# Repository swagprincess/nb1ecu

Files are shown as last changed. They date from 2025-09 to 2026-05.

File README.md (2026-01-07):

# A Speeduino Teensy 4.1 ECU For a NB1 Miata #

Integrated Wideband controller (Spartan 3 OEM), MAP and everything needed for it to be PNP.

Using the current fastest Speeduino brain (Teensy 4.1 600MHz).

Config is a modified init.cpp pinmapping case 56 "Bear Cub", adds default pins for features like AC control

Speeduino.ini for TunerStudio is Case 56, changed name to SwagPrincess NB1 PNP

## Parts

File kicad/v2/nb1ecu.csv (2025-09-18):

Reference | Qty | Value | DNP | Exclude from BOM | Exclude from Board | Footprint | Datasheet | LCSC Part #
C1,C7 | 2 | 100u |  |  |  | Capacitor_THT:CP_Radial_D6.3mm_P2.50mm | ~ | C109392
C2,C21 | 2 | 22n |  |  |  | Capacitor_SMD:C_0805_2012Metric_Pad1.18x1.45mm_HandSolder | ~ | C77069
C3 | 1 | 1n |  |  |  | Capacitor_SMD:C_0805_2012Metric_Pad1.18x1.45mm_HandSolder | ~ | C1791
C4,C6 | 2 | 10u |  |  |  | Capacitor_SMD:C_0805_2012Metric_Pad1.18x1.45mm_HandSolder | ~ | C84416
C5,C8,C13,C15,C18,C19,C20 | 7 | 100n |  |  |  | Capacitor_SMD:C_0805_2012Metric_Pad1.18x1.45mm_HandSolder | ~ | C520083
C9,C10,C12,C14,C16,C17 | 6 | 220n |  |  |  | Capacitor_SMD:C_0805_2012Metric_Pad1.18x1.45mm_HandSolder | ~ | C541527
C11 | 1 | 470n |  |  |  | Capacitor_SMD:C_0805_2012Metric_Pad1.18x1.45mm_HandSolder | ~ | C520079
L1 | 1 | 4.7u |  |  |  | Inductor_SMD:L_1008_2520Metric_Pad1.43x2.20mm_HandSolder | ~ | C82314
P2 | 1 | 178780-1 |  |  |  | 178780-1 | DOCUMENTATION | C5166246
Q1,Q2 | 2 | PN2907A |  |  |  | Package_TO_SOT_THT:TO-92_Inline_Wide | https://www.nteinc.com/specs/original/2N3905_06.pdf | C513106
Q3,Q4,Q5,Q8,Q9,Q10,Q11,Q12,Q13,Q14,Q15,Q16,Q17 | 13 | DMG2302U |  |  |  | Package_TO_SOT_SMD:SOT-23 | http://www.diodes.com/assets/Datasheets/DMG2302U.pdf | C96613
Q6 | 1 | DMG2305UX |  |  |  | Package_TO_SOT_SMD:SOT-23 | ~ | C150470
R1,R13 | 2 | 48.7k |  |  |  | Resistor_SMD:R_0805_2012Metric_Pad1.20x1.40mm_HandSolder | ~ | C865519
R2 | 1 | 330 |  |  |  | Resistor_SMD:R_0805_2012Metric_Pad1.20x1.40mm_HandSolder | ~ | C105878
R3 | 1 | 3.3k |  |  |  | Resistor_SMD:R_0805_2012Metric_Pad1.20x1.40mm_HandSolder | ~ | C114531
R4,R7 | 2 | 3k |  |  |  | Resistor_SMD:R_0805_2012Metric_Pad1.20x1.40mm_HandSolder | ~ | C126350
R5 | 1 | 30k |  |  |  | Resistor_SMD:R_0805_2012Metric_Pad1.20x1.40mm_HandSolder | ~ | C126352
R6,R32,R36,R37,R51 | 5 | 1k |  |  |  | Resistor_SMD:R_0805_2012Metric_Pad1.20x1.40mm_HandSolder | ~ | C727989
R8,R11,R12,R14,R33,R34,R35,R45 | 8 | 10k |  |  |  | Resistor_SMD:R_0805_2012Metric_Pad1.20x1.40mm_HandSolder | ~ | C855098
R9 | 1 | 1M |  |  |  | Resistor_SMD:R_0805_2012Metric_Pad1.20x1.40mm_HandSolder | ~ | C107700
R10 | 1 | 22k |  |  |  | Resistor_SMD:R_0805_2012Metric_Pad1.20x1.40mm_HandSolder | ~ | C114565
R15,R16,R17,R18,R20,R21,R23,R25,R27,R38,R39,R40,R43,R44,R46,R47 | 16 | 180k |  |  |  | Resistor_SMD:R_0805_2012Metric_Pad1.20x1.40mm_HandSolder | ~ | C865232
R19,R31,R50 | 3 | 470 |  |  |  | Resistor_SMD:R_0805_2012Metric_Pad1.20x1.40mm_HandSolder | ~ | C114564
R22,R24,R26,R28 | 4 | 348k |  |  |  | Resistor_SMD:R_0805_2012Metric_Pad1.20x1.40mm_HandSolder | ~ | C228757
R29,R30 | 2 | 2.49k |  |  |  | Resistor_SMD:R_0805_2012Metric_Pad1.20x1.40mm_HandSolder | ~ | C375522
R41,R42 | 2 | 220 |  |  |  | Resistor_SMD:R_0805_2012Metric_Pad1.20x1.40mm_HandSolder | ~ | C114519
R48 | 1 | 3.9k |  |  |  | Resistor_SMD:R_0805_2012Metric_Pad1.20x1.40mm_HandSolder | ~ | C865471
R49 | 1 | 604 |  |  |  | Resistor_SMD:R_0805_2012Metric_Pad1.20x1.40mm_HandSolder | ~ | C472205
U2 | 1 | TL431LP |  |  |  | Package_TO_SOT_THT:TO-92_Inline | http://www.ti.com/lit/ds/symlink/tl431.pdf | C398376
U4,U6 | 2 | TC4424AVOA |  |  |  | TC4424AVOA:SOIC127P599X175-8N |  | C44150
U5 | 1 | AP63205WU |  |  |  | Package_TO_SOT_SMD:TSOT-23-6 | https://www.diodes.com/assets/Datasheets/AP63200-AP63201-AP63203-AP63205.pdf | C2071056
U8 | 1 | MPXHZ6115A |  |  |  | Package_SO:SSOP-8_3.95x5.21x3.27mm_P1.27mm | https://www.nxp.com/docs/en/data-sheet/MPXA6115A.pdf | C3235759
U13 | 1 | LMV324LIDT |  |  |  | Package_SO:SOIC-14_3.9x8.7mm_P1.27mm | http://www.ti.com/lit/ds/symlink/lmv324.pdf | C262920
LAMBDA_OUT1 | 1 | TestPoint |  | Excluded from BOM |  | TestPoint:TestPoint_Pad_3.0x3.0mm | ~
U1 | 1 | Teensy4.1 |  | Excluded from BOM |  | teensy:Teensy41
U3 | 1 | MPX4250 |  | Excluded from BOM |  | mpx:MPX-4_MAP
U7 | 1 | ~ |  | Excluded from BOM |  | spartan3oem:spartan3oem

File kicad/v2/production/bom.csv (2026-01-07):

Designator | Footprint | Quantity | Value | LCSC Part #
C1, C7 | CP_Radial_D6.3mm_P2.50mm | 2 | 100u | C109392
C10, C12, C14, C16, C17, C22, C23, C9 | 0805 | 8 | 220n | C541527
C11 | 0805 | 1 | 470n | C520079
C13, C15, C18, C19, C20, C5, C8 | 0805 | 7 | 100n | C520083
C2, C21 | 0805 | 2 | 22n | C77069
C3 | 0805 | 1 | 1n | C1791
C4, C6 | 0805 | 2 | 10u | C84416
D1, D10, D11, D2, D3, D4, D5, D6, D7, D8, D9 | D_SOD-123 | 11 | 1N4448W | C124191
J1_2 | Molex_Micro-Fit_3.0_43045-0600_2x03_P3.00mm_Horizontal | 1 | Conn_02x03_Top_Bottom | C127367
J2_2 | Molex_Micro-Fit_3.0_43650-0200_1x02_P3.00mm_Horizontal | 1 | Conn_01x02 | C192562
J3_2 | Jack_3.5mm_CUI_SJ1-3525N_Horizontal | 1 | AudioPlug3 | C381120
J4_2 | PinSocket_1x03_P2.54mm_Vertical | 1 | Conn_01x03_Pin
L1 | 1008 | 1 | 4.7u | C82314
P2 | 178780-1 | 1 | 178780-1 | C5166246
Q1, Q2 | TO-92_Inline_Wide | 2 | PN2907A | C903222
Q10, Q11, Q12, Q13, Q14, Q15, Q16, Q17, Q3, Q4, Q5, Q8, Q9 | SOT-23 | 13 | DMG2302U | C96613
Q6 | SOT-23 | 1 | DMG2305UX | C150470
R1, R13 | 0805 | 2 | 48.7k | C865519
R10 | 0805 | 1 | 22k | C114565
R11, R12, R14, R33, R34, R35, R45, R55, R8 | 0805 | 9 | 10k | C855098
R15, R16, R17, R18, R20, R21, R23, R25, R27, R38, R39, R40, R43, R44, R46, R47 | 0805 | 16 | 180k | C865232
R19, R31, R50 | 0805 | 3 | 470 | C114564
R2 | 0805 | 1 | 330 | C105878
R22, R24, R26, R28 | 0805 | 4 | 348k | C228757
R29, R30 | 0805 | 2 | 2.49k | C375522
R3 | 0805 | 1 | 3.3k | C114531
R32, R36, R37, R51, R52, R53, R6 | 0805 | 7 | 1k | C727989
R4, R7 | 0805 | 2 | 3k | C126350
R41, R42 | 0805 | 2 | 220 | C114519
R48 | 0805 | 1 | 3.9k | C865471
R49 | 0805 | 1 | 604 | C472205
R5 | 0805 | 1 | 30k | C126352
R54 | 0805 | 1 | 120 | C727984
R9 | 0805 | 1 | 1M | C107700
U13 | SOIC-14_3.9x8.7mm_P1.27mm | 1 | LMV324LIDT | C262920
U2 | TO-92_Inline | 1 | TL431LP | C398376
U4, U6 | SOIC127P599X175-8N | 2 | TC4424AVOA | C44150
U5 | TSOT-23-6 | 1 | AP63205WU | C2071056
U8 | SSOP-8_3.95x5.21x3.27mm_P1.27mm | 1 | MPXHZ6115A | C3235759
U9 | SOIC-8_3.9x4.9mm_P1.27mm | 1 | SN65HVD232 | C30530

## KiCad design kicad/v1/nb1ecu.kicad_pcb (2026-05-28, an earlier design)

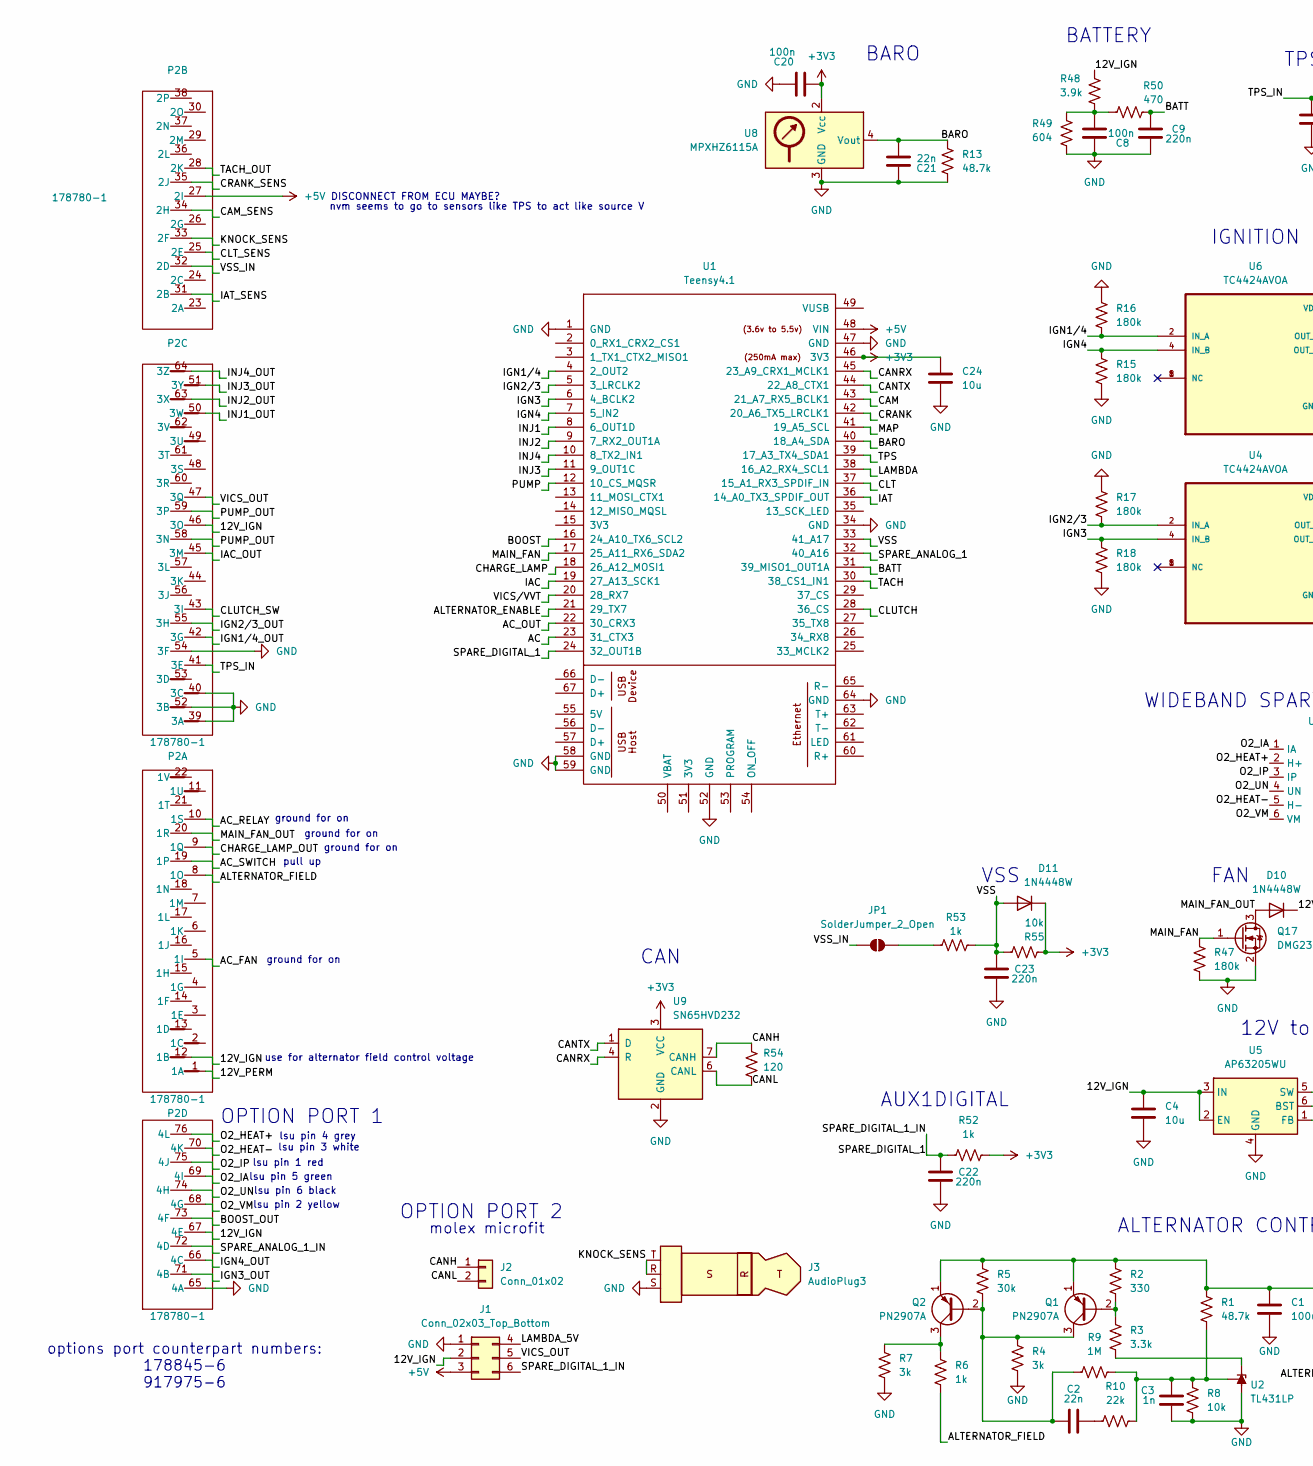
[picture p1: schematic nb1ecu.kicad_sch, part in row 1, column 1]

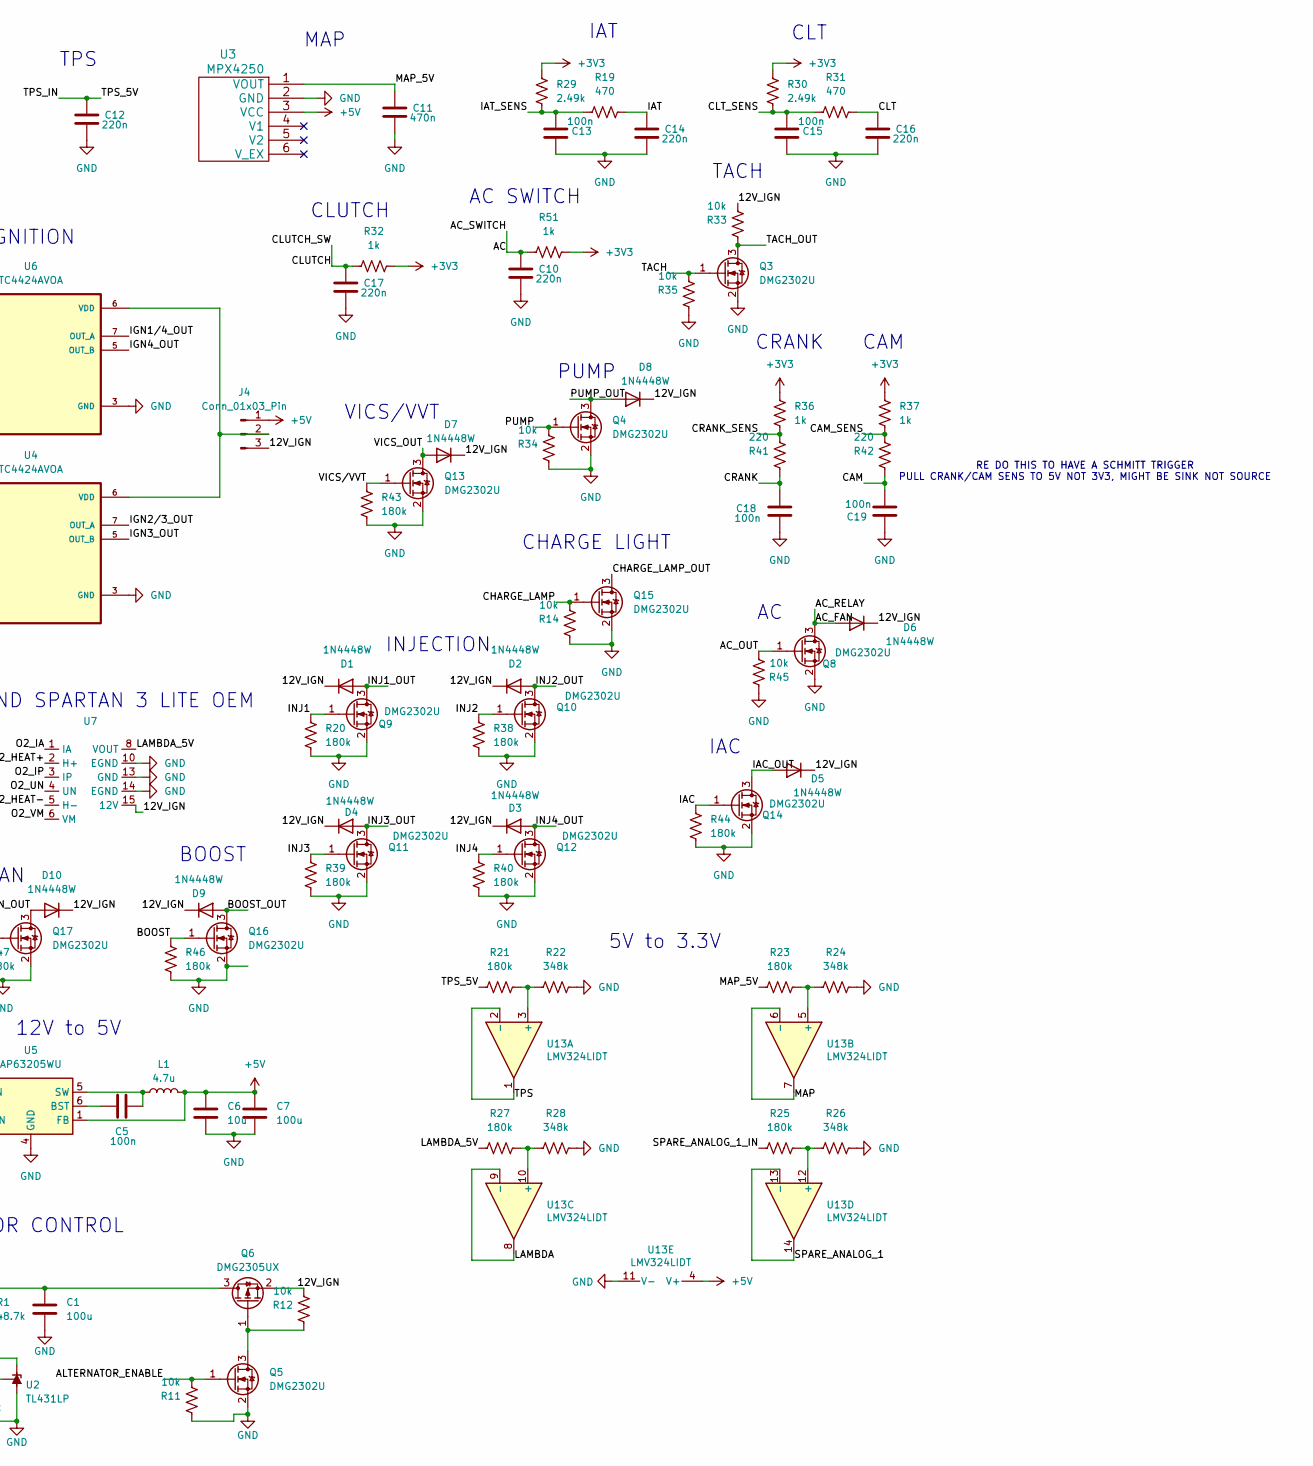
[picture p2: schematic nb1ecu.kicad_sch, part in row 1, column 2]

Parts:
C1, C7: 100u; CP_Radial_D6.3mm_P2.50mm; LCSC Part # C109392
C2, C21: 22n; C_0805_2012Metric_Pad1.18x1.45mm_HandSolder; LCSC Part # C77069
C3: 1n; C_0805_2012Metric_Pad1.18x1.45mm_HandSolder; LCSC Part # C1791
C4, C6, C24: 10u; C_0805_2012Metric_Pad1.18x1.45mm_HandSolder; LCSC Part # C84416
C5, C8, C13, C15, C18, C19, C20: 100n; C_0805_2012Metric_Pad1.18x1.45mm_HandSolder; LCSC Part # C520083
C9, C10, C12, C14, C16, C17, C22, C23: 220n; C_0805_2012Metric_Pad1.18x1.45mm_HandSolder; LCSC Part # C541527
C11: 470n; C_0805_2012Metric_Pad1.18x1.45mm_HandSolder; LCSC Part # C520079
D1, D2, D3, D4, D5, D6, D7, D8, D9, D10, D11: 1N4448W; D_SOD-123; LCSC Part # C124191
J1: Conn_02x03_Top_Bottom; Molex_Micro-Fit_3.0_43045-0600_2x03_P3.00mm_Horizontal; LCSC Part # C127367
J2: Conn_01x02; Molex_Micro-Fit_3.0_43650-0200_1x02_P3.00mm_Horizontal; LCSC Part # C192562
J3: AudioPlug3; Jack_3.5mm_CUI_SJ1-3525N_Horizontal; LCSC Part # C381120
J4: Conn_01x03_Pin; PinSocket_1x03_P2.54mm_Vertical
JP1: SolderJumper_2_Open; SolderJumper-2_P1.3mm_Open_Pad1.0x1.5mm
L1: 4.7u; L_1008_2520Metric_Pad1.43x2.20mm_HandSolder; LCSC Part # C82314
P2: 178780-1; LCSC Part # C5166246
Q1, Q2: PN2907A; TO-92_Inline_Wide; LCSC Part # C903222
Q3, Q4, Q5, Q8, Q9, Q10, Q11, Q12, Q13, Q14, Q15, Q16, Q17: DMG2302U; SOT-23; LCSC Part # C96613
Q6: DMG2305UX; SOT-23; LCSC Part # C150470
R1, R13: 48.7k; R_0805_2012Metric_Pad1.20x1.40mm_HandSolder; LCSC Part # C865519
R2: 330; R_0805_2012Metric_Pad1.20x1.40mm_HandSolder; LCSC Part # C105878
R3: 3.3k; R_0805_2012Metric_Pad1.20x1.40mm_HandSolder; LCSC Part # C114531
R4, R7: 3k; R_0805_2012Metric_Pad1.20x1.40mm_HandSolder; LCSC Part # C126350
R5: 30k; R_0805_2012Metric_Pad1.20x1.40mm_HandSolder; LCSC Part # C126352
R6, R32, R36, R37, R51, R52, R53: 1k; R_0805_2012Metric_Pad1.20x1.40mm_HandSolder; LCSC Part # C727989
R8, R11, R12, R14, R33, R34, R35, R45, R55: 10k; R_0805_2012Metric_Pad1.20x1.40mm_HandSolder; LCSC Part # C855098
R9: 1M; R_0805_2012Metric_Pad1.20x1.40mm_HandSolder; LCSC Part # C107700
R10: 22k; R_0805_2012Metric_Pad1.20x1.40mm_HandSolder; LCSC Part # C114565
R15, R16, R17, R18, R20, R21, R23, R25, R27, R38, R39, R40, R43, R44, R46, R47: 180k; R_0805_2012Metric_Pad1.20x1.40mm_HandSolder; LCSC Part # C865232
R19, R31, R50: 470; R_0805_2012Metric_Pad1.20x1.40mm_HandSolder; LCSC Part # C114564
R22, R24, R26, R28: 348k; R_0805_2012Metric_Pad1.20x1.40mm_HandSolder; LCSC Part # C228757
R29, R30: 2.49k; R_0805_2012Metric_Pad1.20x1.40mm_HandSolder; LCSC Part # C375522
R41, R42: 220; R_0805_2012Metric_Pad1.20x1.40mm_HandSolder; LCSC Part # C114519
R48: 3.9k; R_0805_2012Metric_Pad1.20x1.40mm_HandSolder; LCSC Part # C865471
R49: 604; R_0805_2012Metric_Pad1.20x1.40mm_HandSolder; LCSC Part # C472205
R54: 120; R_0805_2012Metric_Pad1.20x1.40mm_HandSolder; LCSC Part # C727984
U1: Teensy4.1; Teensy41
U2: TL431LP; TO-92_Inline; LCSC Part # C398376
U3: MPX4250; MPX-4_MAP
U4, U6: TC4424AVOA; SOIC127P599X175-8N; LCSC Part # C44150
U5: AP63205WU; TSOT-23-6; LCSC Part # C2071056
U7: spartan3oem
U8: MPXHZ6115A; SSOP-8_3.95x5.21x3.27mm_P1.27mm; LCSC Part # C3235759
U9: SN65HVD232; SOIC-8_3.9x4.9mm_P1.27mm; LCSC Part # C30530
U13: LMV324LIDT; SOIC-14_3.9x8.7mm_P1.27mm; Manufacturer_Part_Number LMV324LIDT; Digikey Part Number 497-13052-1-ND

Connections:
+3V3: C20.2, C24.1, D11.1 (K), R29.1, R30.1, R32.2, R36.2, R37.2, R51.2, R52.2, R55.1, U1.46 (3V3), U8.2 (Vcc), U9.3 (VCC)
+5V: C6.1, C7.1, J1.3, J4.1, L1.2, P2.27 (2I), U1.48 (VIN), U3.3 (VCC), U5.1 (FB), U13.4 (V+)
/12V_IGN: C4.1, D1.1 (K), D2.1 (K), D3.1 (K), D4.1 (K), D5.1 (K), D6.1 (K), D7.1 (K), D8.1 (K), D9.1 (K), D10.1 (K), J1.2, J4.3, P2.12 (1B), P2.46 (3O), P2.67 (4E), Q6.2 (S), R12.1, R33.1, R48.2, U5.2 (EN), U5.3 (IN), U7.15 (12V)
/12V_PERM: P2.1 (1A)
/AC: C10.1, P2.19 (1P), R51.1, U1.23 (31_CTX3)
/AC_FAN: D6.2 (A), P2.5 (1I), P2.10 (1S), Q8.3 (D)
/AC_OUT: Q8.1 (G), R45.2, U1.22 (30_CRX3)
/ALTERNATOR_ENABLE: Q5.1 (G), R11.1, U1.21 (29_TX7)
/ALTERNATOR_FIELD: P2.8 (1O), R6.2
/BARO: C21.2, R13.1, U1.40 (18_A4_SDA), U8.4 (Vout)
/BATT: C9.1, R50.1, U1.31 (39_MISO1_OUT1A)
/BOOST: Q16.1 (G), R46.2, U1.16 (24_A10_TX6_SCL2)
/BOOST_OUT: D9.2 (A), P2.73 (4F), Q16.3 (D)
/CAM: C19.2, R42.2, U1.43 (21_A7_RX5_BCLK1)
/CAM_SENS: P2.34 (2H), R37.1, R42.1
/CANH: J2.1, R54.1, U9.7 (CANH)
/CANL: J2.2, R54.2, U9.6 (CANL)
/CANRX: U1.45 (23_A9_CRX1_MCLK1), U9.4 (R)
/CANTX: U1.44 (22_A8_CTX1), U9.1 (D)
/CHARGE_LAMP: Q15.1 (G), R14.1, U1.18 (26_A12_MOSI1)
/CHARGE_LAMP_OUT: P2.9 (1Q), Q15.3 (D)
/CLT: C16.1, R31.1, U1.37 (15_A1_RX3_SPDIF_IN)
/CLT_SENS: C15.1, P2.25 (2E), R30.2, R31.2
/CLUTCH: C17.1, P2.43 (3I), R32.1, U1.28 (36_CS)
/CRANK: C18.2, R41.2, U1.42 (20_A6_TX5_LRCLK1)
/CRANK_SENS: P2.35 (2J), R36.1, R41.1
/IAC: Q14.1 (G), R44.2, U1.19 (27_A13_SCK1)
/IAC_OUT: D5.2 (A), P2.45 (3M), Q14.3 (D)
/IAT: C14.1, R19.1, U1.36 (14_A0_TX3_SPDIF_OUT)
/IAT_SENS: C13.1, P2.31 (2B), R19.2, R29.2
/IGN1/4: R16.1, U1.4 (2_OUT2), U6.2 (IN_A)
/IGN1/4_OUT: P2.42 (3G), U6.7 (OUT_A)
/IGN2/3: R17.1, U1.5 (3_LRCLK2), U4.2 (IN_A)
/IGN2/3_OUT: P2.55 (3H), U4.7 (OUT_A)
/IGN3: R18.2, U1.6 (4_BCLK2), U4.4 (IN_B)
/IGN3_OUT: P2.71 (4B), U4.5 (OUT_B)
/IGN4: R15.2, U1.7 (5_IN2), U6.4 (IN_B)
/IGN4_OUT: P2.66 (4C), U6.5 (OUT_B)
/INJ1: Q9.1 (G), R20.2, U1.8 (6_OUT1D)
/INJ1_OUT: D1.2 (A), P2.50 (3W), Q9.3 (D)
/INJ2: Q10.1 (G), R38.2, U1.9 (7_RX2_OUT1A)
/INJ2_OUT: D2.2 (A), P2.63 (3X), Q10.3 (D)
/INJ3: Q11.1 (G), R39.2, U1.11 (9_OUT1C)
/INJ3_OUT: D4.2 (A), P2.51 (3Y), Q11.3 (D)
/INJ4: Q12.1 (G), R40.2, U1.10 (8_TX2_IN1)
/INJ4_OUT: D3.2 (A), P2.64 (3Z), Q12.3 (D)
/KNOCK_SENS: J3.R, J3.T, P2.33 (2F); also elsewhere on the board
/LAMBDA: U1.38 (16_A2_RX4_SCL1), U13.8, U13.9 (-)
/LAMBDA_5V: J1.4, R27.1, U7.8 (VOUT)
/MAIN_FAN: Q17.1 (G), R47.2, U1.17 (25_A11_RX6_SDA2)
/MAIN_FAN_OUT: D10.2 (A), P2.20 (1R), Q17.3 (D)
/MAP: U1.41 (19_A5_SCL), U13.6 (-), U13.7
/MAP_5V: C11.1, R23.1, U3.1 (VOUT)
/O2_HEAT+: P2.76 (4L), U7.2 (H+)
/O2_HEAT-: P2.70 (4K), U7.5 (H-)
/O2_IA: P2.69 (4I), U7.1 (IA)
/O2_IP: P2.75 (4J), U7.3 (IP)
/O2_UN: P2.74 (4H), U7.4 (UN)
/O2_VM: P2.68 (4G), U7.6 (VM)
/PUMP: Q4.1 (G), R34.1, U1.12 (10_CS_MQSR)
/PUMP_OUT: D8.2 (A), P2.58 (3N), P2.59 (3P), Q4.3 (D)
/SPARE_ANALOG_1: U1.32 (40_A16), U13.13 (-), U13.14
/SPARE_ANALOG_1_IN: P2.72 (4D), R25.1
/SPARE_DIGITAL_1: C22.1, J1.6, R52.1, U1.24 (32_OUT1B)
/TACH: Q3.1 (G), R35.1, U1.30 (38_CS1_IN1)
/TACH_OUT: P2.28 (2K), Q3.3 (D), R33.2
/TPS: U1.39 (17_A3_TX4_SDA1), U13.1, U13.2 (-)
/TPS_5V: C12.1, P2.41 (3E), R21.1
/VICS_OUT: D7.2 (A), J1.5, P2.47 (3Q), Q13.3 (D)
/VICS/VVT: Q13.1 (G), R43.2, U1.20 (28_RX7)
/VSS: C23.1, D11.2 (A), R53.2, R55.2, U1.33 (41_A17)
/VSS_IN: JP1.1 (A), P2.32 (2D)
GND: C1.2, C3.1, C4.2, C6.2, C7.2, C8.2, C9.2, C10.2, C11.2, C12.2, C13.2, C14.2, C15.2, C16.2, C17.2, C18.1, C19.1, C20.1, C21.1, C22.2, C23.2, C24.2, J1.1, J3.1, J3.S, P2.39 (3A), P2.40 (3C), P2.52 (3B), P2.54 (3F), P2.65 (4A), Q3.2 (S), Q4.2 (S), Q5.2 (S), Q8.2 (S), Q9.2 (S), Q10.2 (S), Q11.2 (S), Q12.2 (S), Q13.2 (S), Q14.2 (S), Q15.2 (S), Q16.2 (S), Q17.2 (S), R4.2, R7.2, R8.2, R11.2, R13.2, R14.2, R15.1, R16.2, R17.2, R18.1, R20.1, R22.2, R24.2, R26.2, R28.2, R34.2, R35.2, R38.1, R39.1, R40.1, R43.1, R44.1, R45.1, R46.1, R47.1, R49.1, U1.1 (GND), U1.34 (GND), U1.47 (GND), U1.52 (GND), U1.58 (GND), U1.59 (GND), U1.64 (GND), U2.2 (A), U3.2 (GND), U4.3 (GND), U5.4 (GND), U6.3 (GND), U7.10 (EGND), U7.13 (GND), U7.14 (EGND), U8.3 (GND), U9.2 (GND), U13.11 (V-); also elsewhere on the board
unnamed: C2.2, R10.1
unnamed: C8.1, R48.1, R49.2, R50.2
unnamed: J4.2, U4.6 (VDD), U6.6 (VDD)
unnamed: JP1.2 (B), R53.1
unnamed: Q1.2 (B), R2.2, R3.1
unnamed: C2.1, Q1.3 (C), Q2.2 (B), R4.1, R5.2, R9.1
unnamed: C1.1, Q1.1 (E), Q2.1 (E), Q6.3 (D), R1.1, R2.1, R5.1
unnamed: Q2.3 (C), R6.1, R7.1
unnamed: Q5.3 (D), Q6.1 (G), R12.2
unnamed: R3.2, U2.3 (K)
unnamed: C3.2, R1.2, R8.1, R9.2, R10.2, U2.1 (REF)
unnamed: C5.2, U5.6 (BST)
unnamed: C5.1, L1.1, U5.5 (SW)
unnamed: R21.2, R22.1, U13.3 (+)
unnamed: R23.2, R24.1, U13.5 (+)
unnamed: R27.2, R28.1, U13.10 (+)
unnamed: R25.2, R26.1, U13.12 (+)

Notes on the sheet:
ground for on
TPS
options port counterpart numbers: 178845-6 917975-6
BATTERY
WIDEBAND SPARTAN 3 LITE OEM
VICS/VVT
CHARGE LIGHT
AUX1DIGITAL
IGNITION
ALTERNATOR CONTROL
IAC
CAM
CLUTCH
VSS
CAN
use for alternator field control voltage
TACH
lsu pin 1 red
lsu pin 3 white
AC SWITCH
RE DO THIS TO HAVE A SCHMITT TRIGGER PULL CRANK/CAM SENS TO 5V NOT 3V3, MIGHT BE SINK NOT SOURCE
OPTION PORT 2
PUMP
lsu pin 4 grey
12V to 5V
lsu pin 2 yellow
BOOST
OPTION PORT 1
MAP
IAT
INJECTION
CRANK
CLT
DISCONNECT FROM ECU MAYBE?
lsu pin 5 green
5V to 3.3V
BARO
pull up
nvm seems to go to sensors like TPS to act like source V
molex microfit

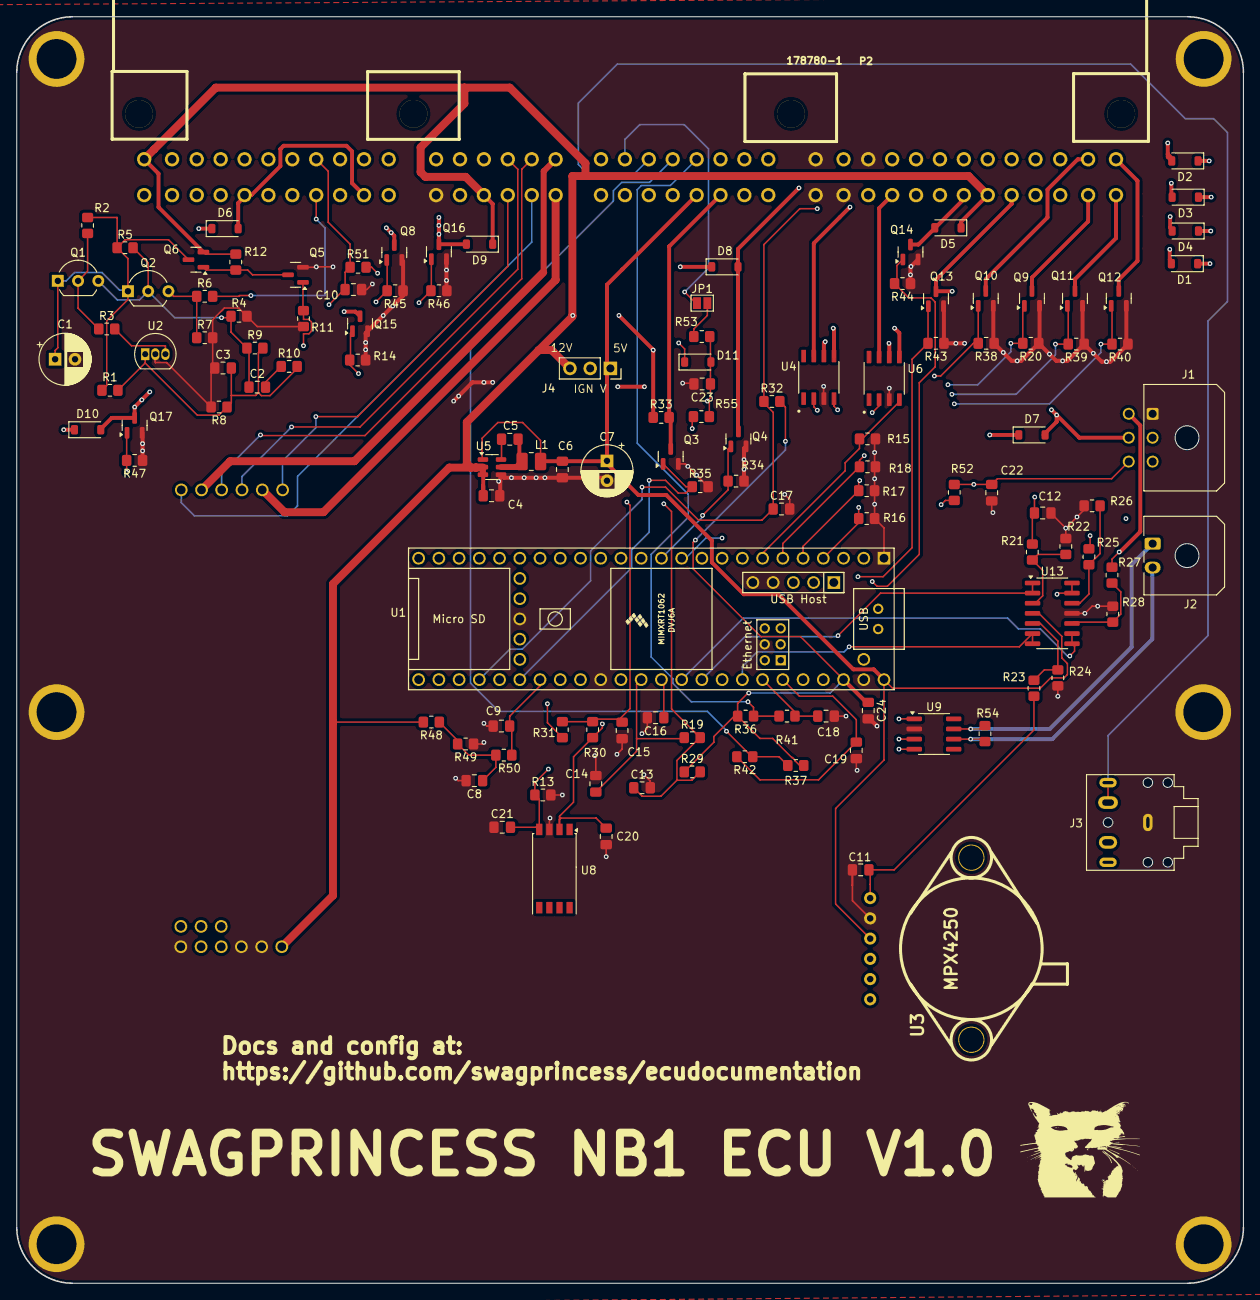
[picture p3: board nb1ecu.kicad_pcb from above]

Board: 4 copper layers, 154.0 x 159.0 mm, 129 parts (0 on the bottom side), 89 nets.

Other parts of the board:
J1#2, J2#2, J4#2, J5, J6: Conn_01x01; MountingHole_4.5mm_Pad
J3#2: AudioPlug3; Jack_3.5mm_CUI_SJ1-3525N_Horizontal

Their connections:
/KNOCK_SENS: J3#2.R, J3#2.T; also elsewhere on the board
GND: J1#2.1, J2#2.1, J3#2.S, J4#2.1, J5.1, J6.1; also elsewhere on the board

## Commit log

2025-09-17 ready to test, need to add part numbers for bom
    [TC4424AVOA.step, nb1ecu.kicad_pcb, nb1ecu.kicad_sch]
2025-09-17 boost control instead of lambda output on connector and other fixes
    [nb1ecu.kicad_pcb, nb1ecu.kicad_sch]
2025-09-18 bunch of new features
    [bom.csv, designators.csv, nb1ecu.csv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]
2025-09-20 options connector
    [nb1ecu.kicad_pcb, nb1ecu.kicad_sch]
2025-09-29 add CANBUS
    [nb1ecu.kicad_pcb, nb1ecu.kicad_sch]
2026-01-07 Official V1.0 milestone, all parts ordered
    [bom.csv, designators.csv, nb1ecu.kicad_pcb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]
2026-05-28 v2 preparation
    [bom.csv, designators.csv, nb1ecu.csv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]
